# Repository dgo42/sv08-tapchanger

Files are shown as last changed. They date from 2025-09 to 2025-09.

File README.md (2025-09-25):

# Rebuild Sovol SV08 to use Tapchanger and up to 6 Toolheads
Sovol SV08 modification to use up to 6 print heads using TapChanger &amp; DragonBurner

1. First I've changed the LCD from the original to the BTT HDMI5. I've used the [BTT HDMI5 enclosure](https://www.printables.com/model/946297-sovol-sv08-btt-hdmi-5-v12-enclosure-compatible). I'm not really happy with this enclosure because of not working LCD buttons and too much backlash between enclosure and the cover frame, but it very robust and do the job. Other deal with this enclosure - it doesn't holds on the SV08 enclosure. You need TPU stopper [STL](https://github.com/dgo42/sv08-tapchanger/tree/main/stls/display) to prevent the screen enclosure to slide up and separate from the SV08 enclosure.

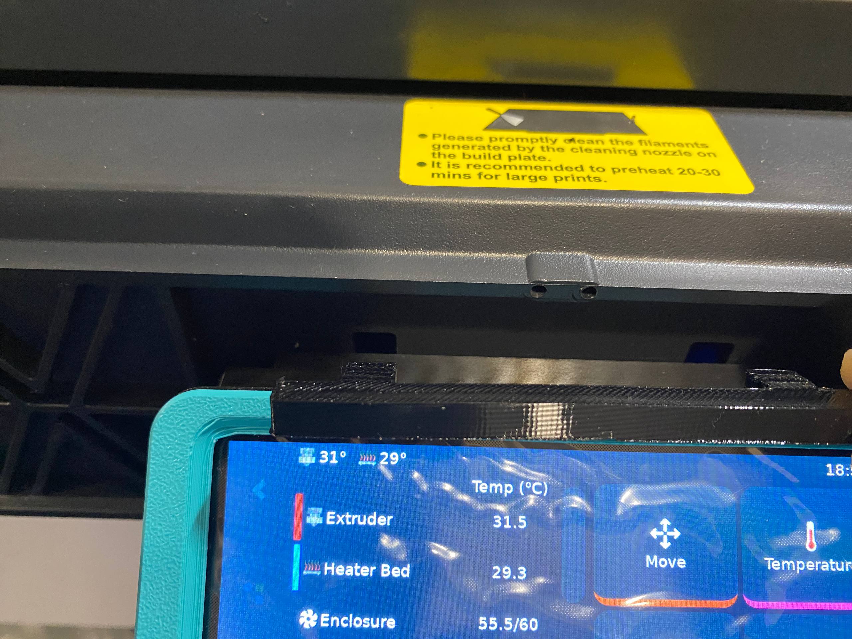
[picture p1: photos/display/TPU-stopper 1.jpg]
   [](https://github.com/dgo42/sv08-tapchanger/tree/main/photos/display/TPU-stopper%201.jpg?raw=true)
   [](https://github.com/dgo42/sv08-tapchanger/tree/main/photos/display/TPU-stopper%201.jpg?raw=true)
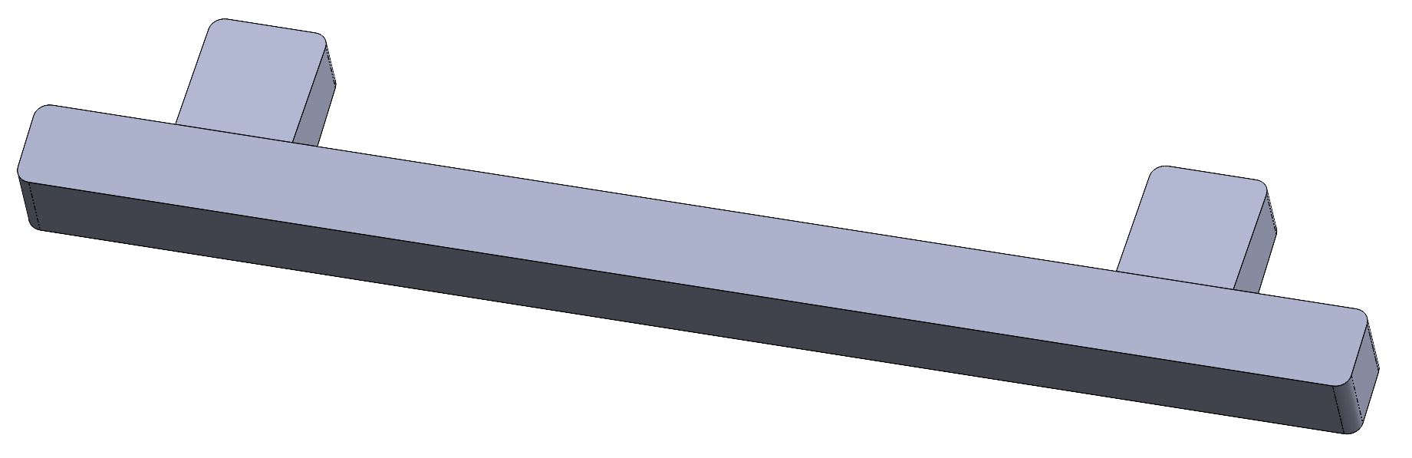
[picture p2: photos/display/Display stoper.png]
   [](https://github.com/dgo42/sv08-tapchanger/tree/main/photos/display/Display%20stoper.png?raw=true)
2. To connect BTT HDMI5 screen I've used original USB cable, but I've connected through [small USB hub](https://www.amazon.de/dp/B0BMXDGSGS) to one of USB type A connectors on the main board. HDMI connector on the main board is only one and it is accessible only from outside. So I've found [180° HDMI adapter](https://www.amazon.de/dp/B0C9DV6ZS) and [flat HDMI cable with 90° connector](https://www.amazon.de/dp/B07R4CPX7V). To use 180° HDMI adapter I needed to make some small cut in the SV08 enclosure.

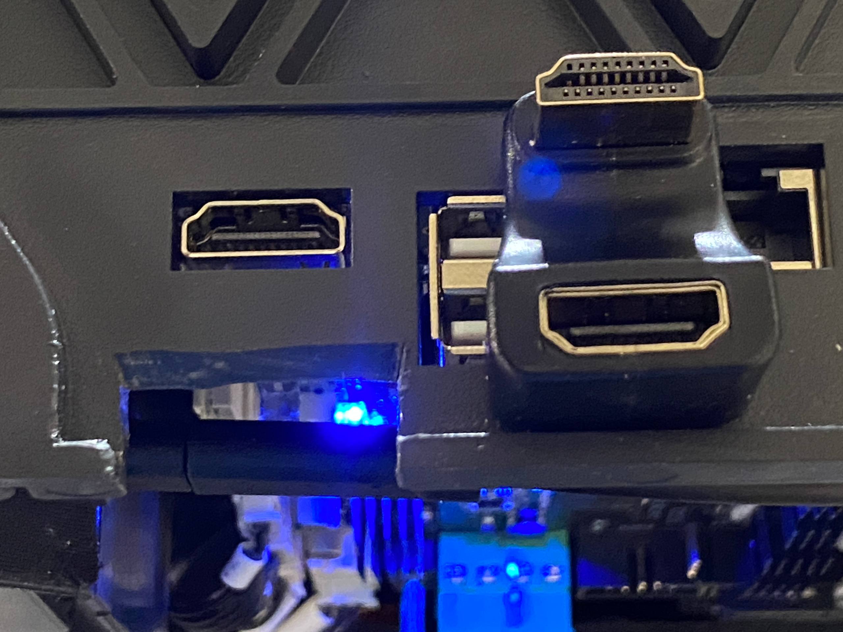
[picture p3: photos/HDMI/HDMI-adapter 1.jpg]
   [](https://github.com/dgo42/sv08-tapchanger/tree/main/photos/HDMI/HDMI-adapter%201.jpg?raw=true)
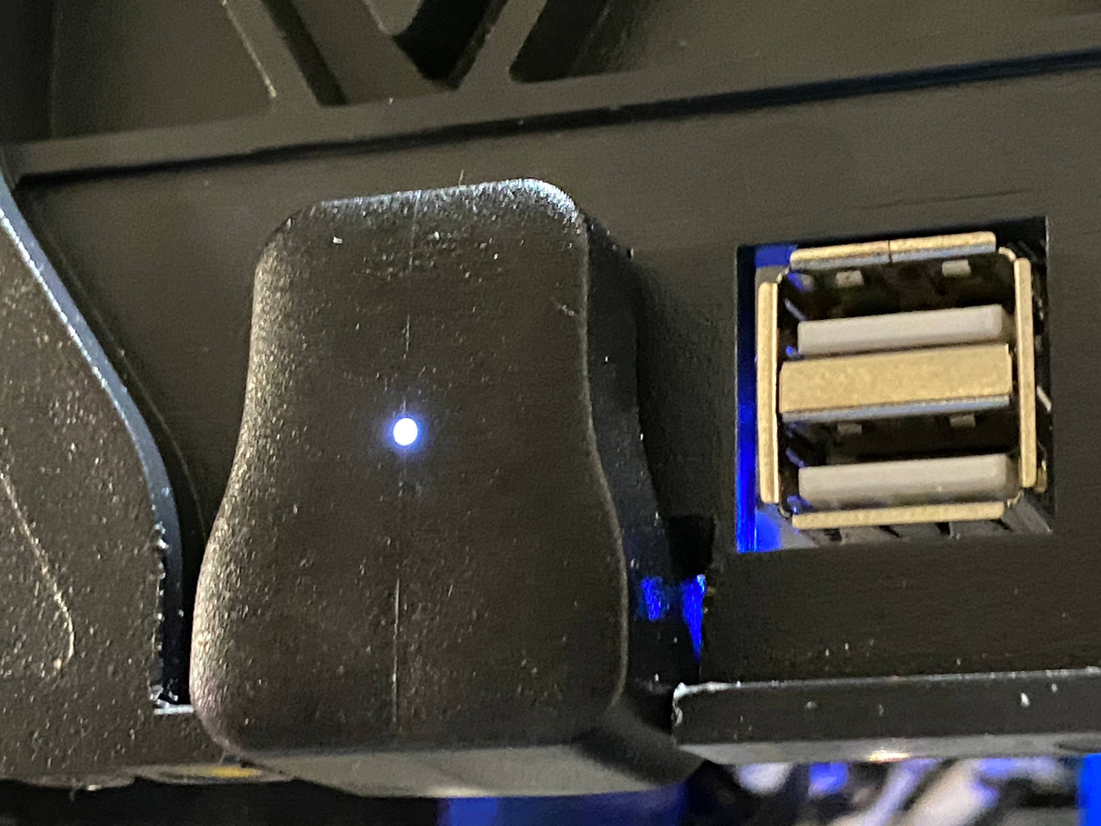
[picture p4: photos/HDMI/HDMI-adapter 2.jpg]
   [](https://github.com/dgo42/sv08-tapchanger/tree/main/photos/HDMI/HDMI-adapter%202.jpg?raw=true)
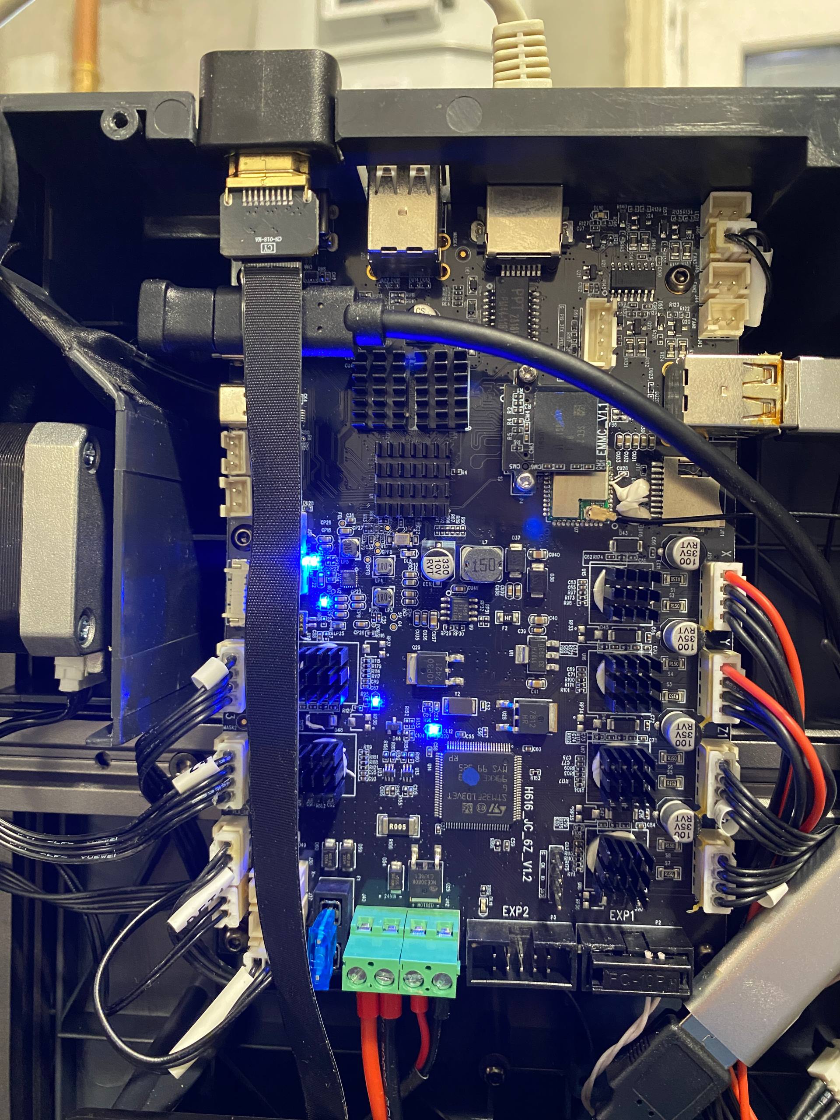
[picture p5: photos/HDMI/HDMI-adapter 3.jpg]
   [](https://github.com/dgo42/sv08-tapchanger/tree/main/photos/HDMI/HDMI-adapter%203.jpg?raw=true)
3. For the future use of up to 6 print heads the original PSU 24V 150W is not enough. I've buyed a cheaper Meanwell RSP-500-24 and made custom holders for [DIN rails](https://www.amazon.de/dp/B09VQ6KJ6H). You need about 266 mm DIN rail and following printed parts [STL](https://github.com/dgo42/sv08-tapchanger/tree/main/stls/psu-mount)

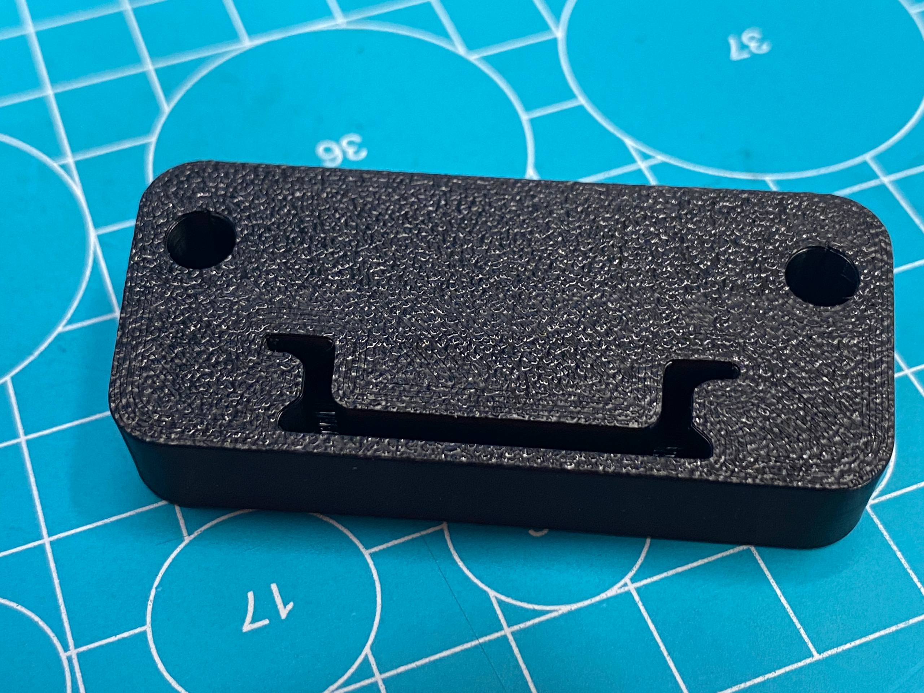
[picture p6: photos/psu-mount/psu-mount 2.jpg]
   [](https://github.com/dgo42/sv08-tapchanger/tree/main/photos/psu-mount/psu-mount%202.jpg?raw=true)
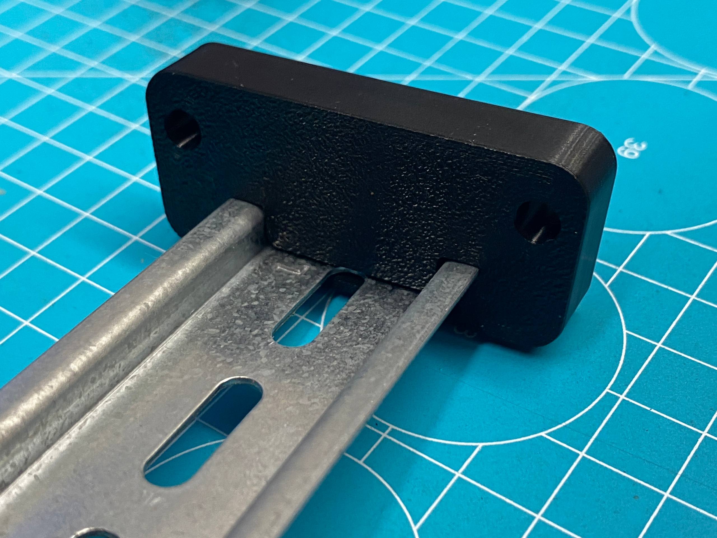
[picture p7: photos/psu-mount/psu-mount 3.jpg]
   [](https://github.com/dgo42/sv08-tapchanger/tree/main/photos/psu-mount/psu-mount%203.jpg?raw=true)
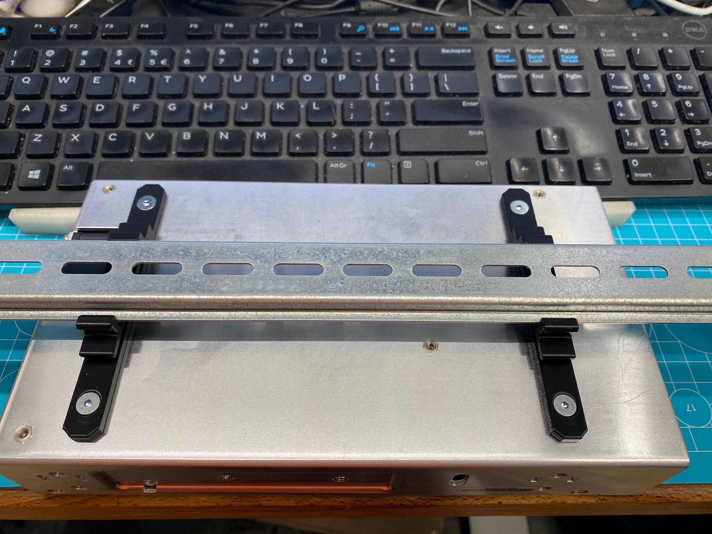
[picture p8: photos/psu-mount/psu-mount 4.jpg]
   [](https://github.com/dgo42/sv08-tapchanger/tree/main/photos/psu-mount/psu-mount%204.jpg?raw=true)
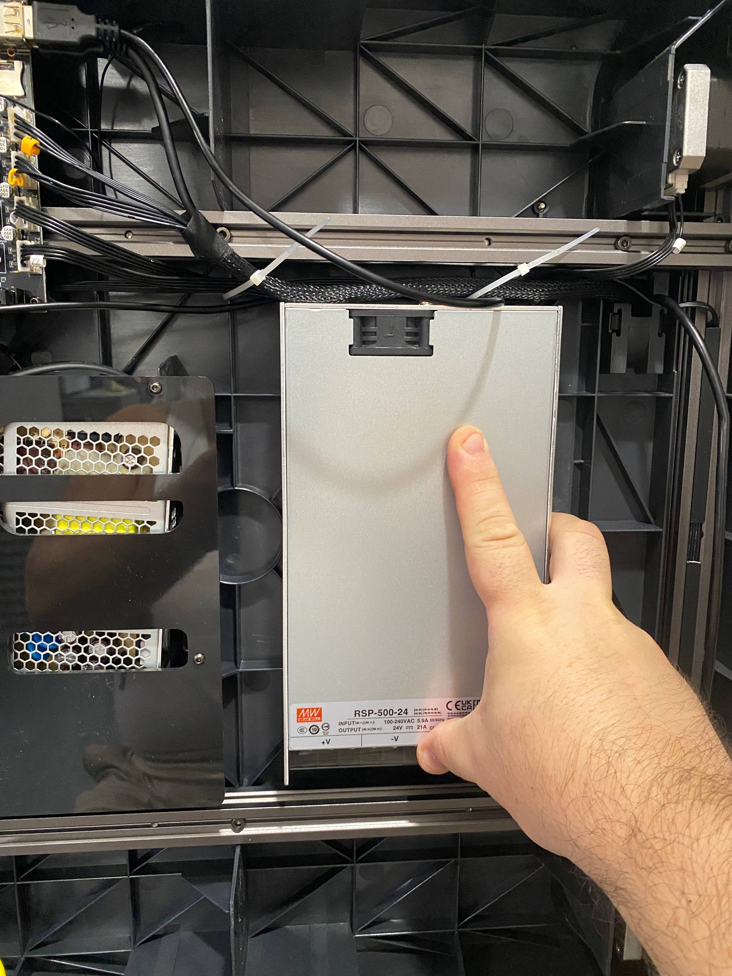
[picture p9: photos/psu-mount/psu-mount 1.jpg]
   [](https://github.com/dgo42/sv08-tapchanger/tree/main/photos/psu-mount/psu-mount%201.jpg?raw=true)
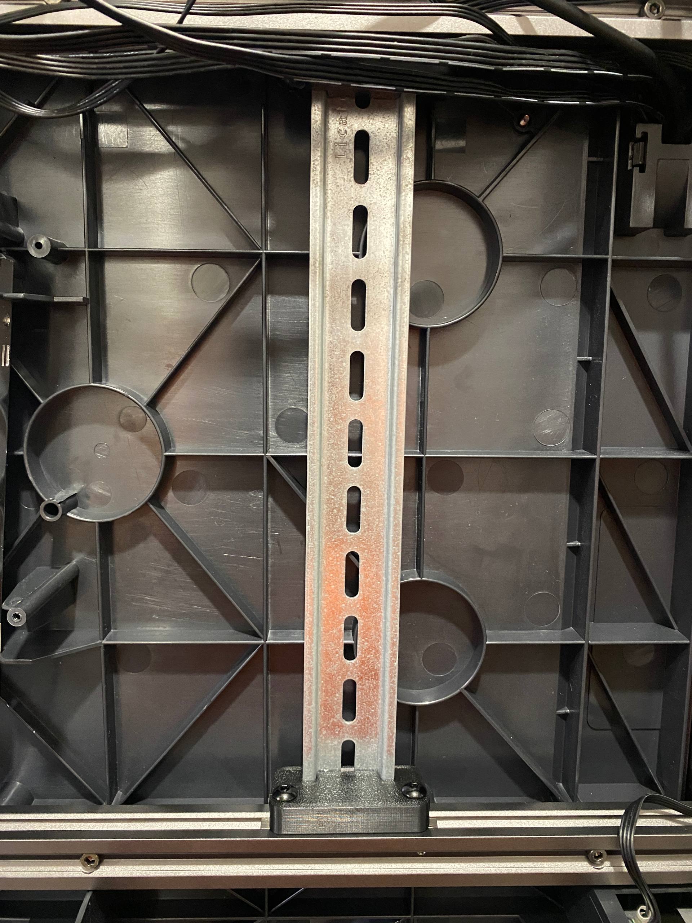
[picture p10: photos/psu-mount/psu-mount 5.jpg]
   [](https://github.com/dgo42/sv08-tapchanger/tree/main/photos/psu-mount/psu-mount%205.jpg?raw=true)
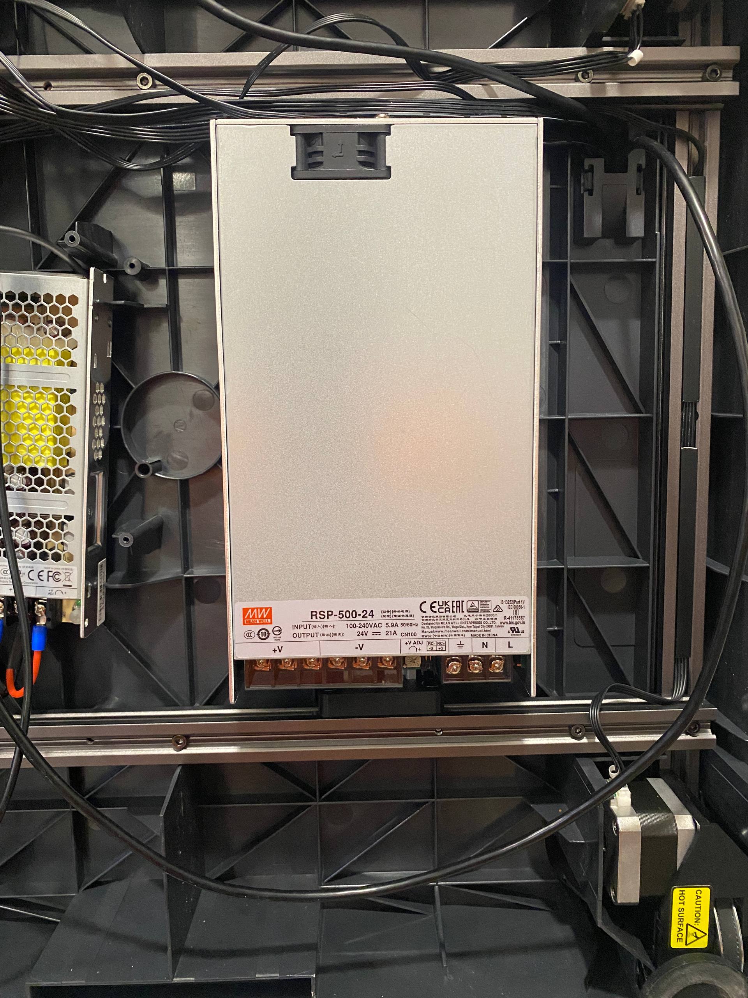
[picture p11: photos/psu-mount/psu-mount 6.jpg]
   [](https://github.com/dgo42/sv08-tapchanger/tree/main/photos/psu-mount/psu-mount%206.jpg?raw=true)
4. To organize the cables underneath I've used the voron deck support as a [cable organiser](https://github.com/dgo42/sv08-tapchanger/tree/main/stls/panels/cable-organiser_x4.stl)

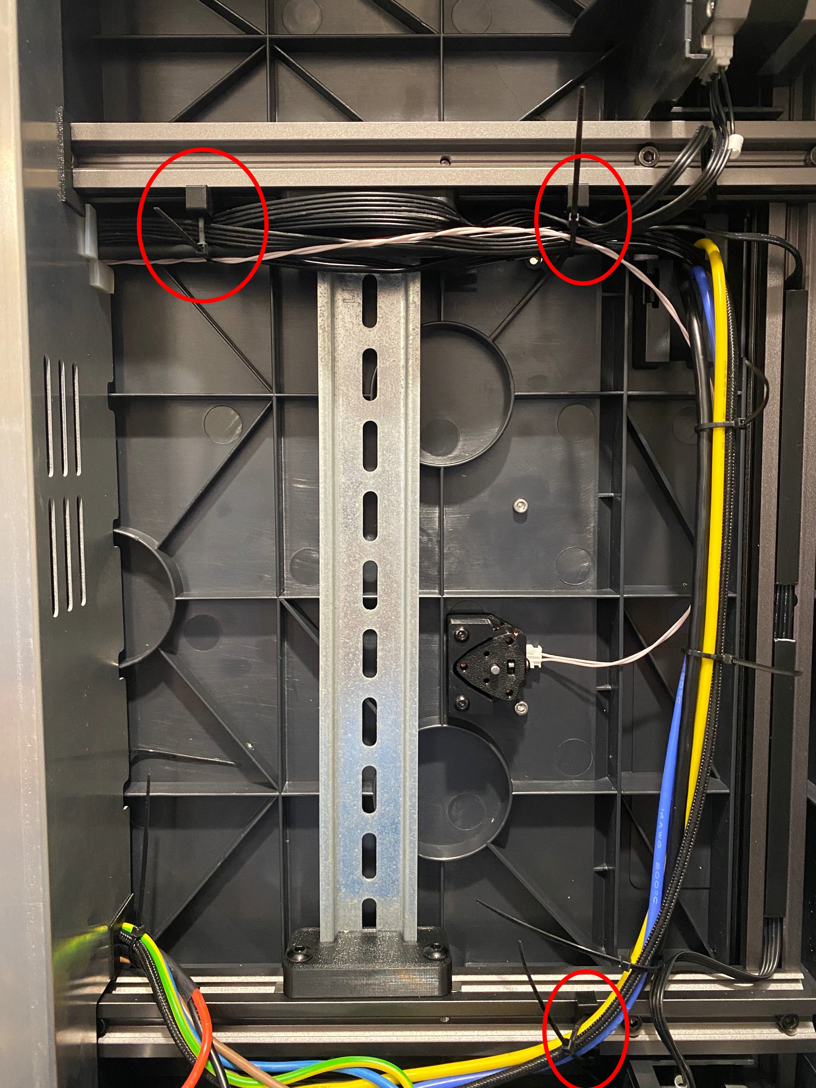
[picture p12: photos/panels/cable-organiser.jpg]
   [](https://github.com/dgo42/sv08-tapchanger/tree/main/photos/panels/cable-organiser.jpg?raw=true)
   
   To ptotect cables underneath aluminium cover I've created this two printed parts [STLs](https://github.com/dgo42/sv08-tapchanger/tree/main/stls/cable-protection) :

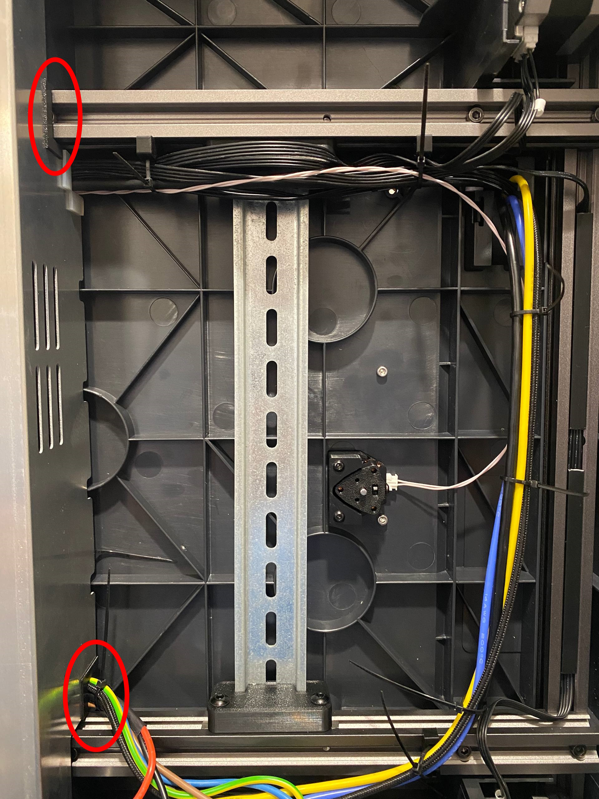
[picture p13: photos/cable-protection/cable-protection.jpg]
   [](https://github.com/dgo42/sv08-tapchanger/tree/main/photos/cable-protection/cable-protection.jpg?raw=true)
5. For different tasks Z-endstop, Z-calibration and XYZ multi printhead calibration I've used the Nudge sensor with 3 mm rod 55 mm long because prinhead has small moving distance behind the bed.
   * To mount the Nudge sensor and custom nozzle wiper I've made special jig to bore the mounting and Nudge rod holes [STL](https://github.com/dgo42/sv08-tapchanger/tree/main/stls/nudge/boring-jig.STL)
 
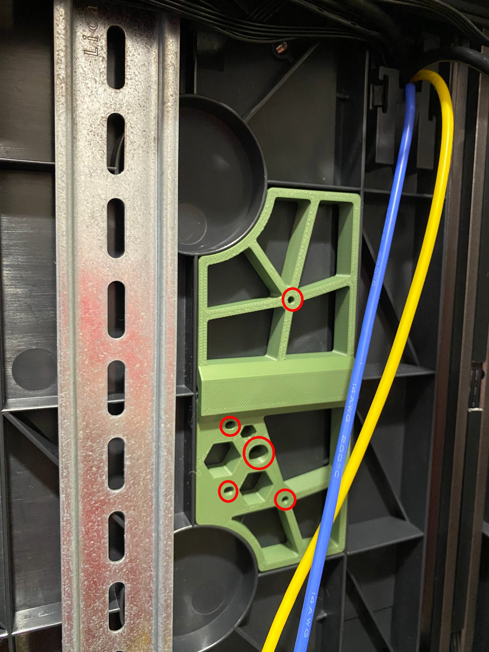
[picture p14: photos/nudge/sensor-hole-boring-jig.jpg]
      [](https://github.com/dgo42/sv08-tapchanger/tree/main/photos/nudge/sensor-hole-boring-jig.jpg?raw=true)
   * I've used modified Nudge sensor body to mount it to the top surface I've added 1mm so that JST XH connector is not outradged [STL](https://github.com/dgo42/sv08-tapchanger/tree/main/stls/nudge/nudge/nudge_2020_sovol.STL)
 
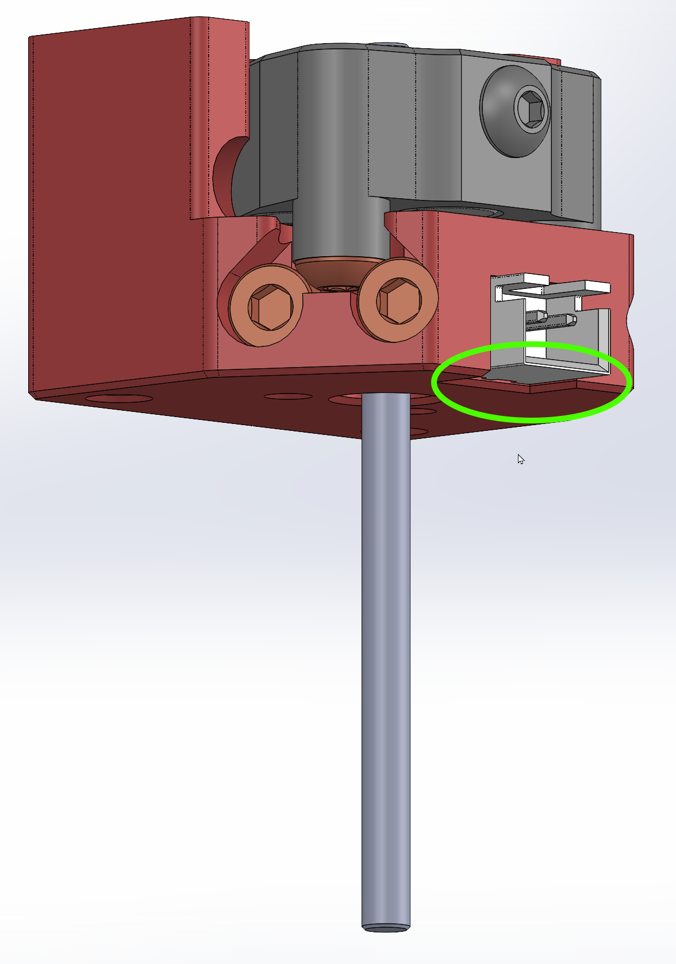
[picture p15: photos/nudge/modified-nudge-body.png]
      [](https://github.com/dgo42/sv08-tapchanger/tree/main/photos/nudge/modified-nudge-body.png?raw=true)
   * Nudge sensor mounted using two washers and 30mm iso 7380-1 screws, two 10mm DIN 912 screws holds other two corners of the nozzle wipper holder.
 
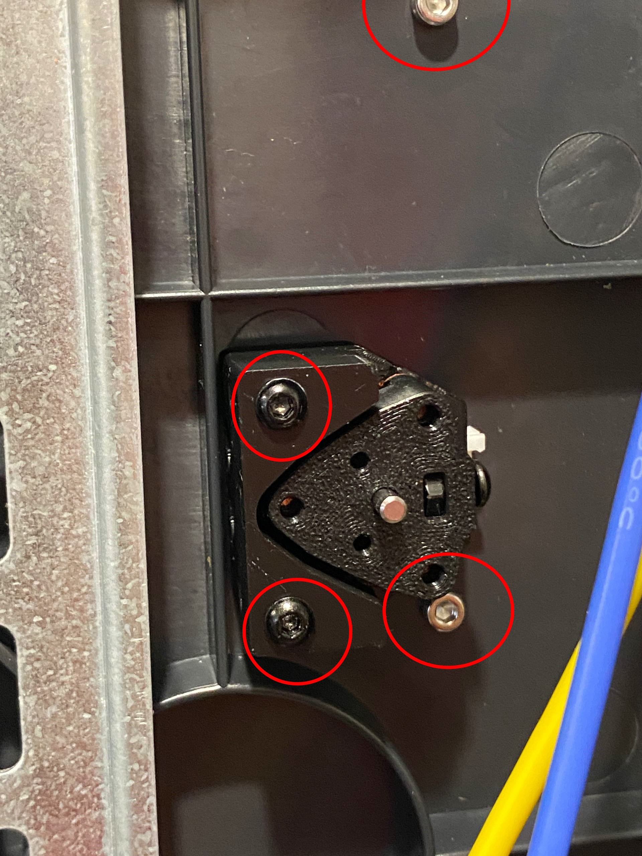
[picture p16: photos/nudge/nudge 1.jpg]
      [](https://github.com/dgo42/sv08-tapchanger/tree/main/photos/nudge/nudge%201.jpg?raw=true)
   * Bambulab A1 silicone nozzle wiper (for example https://www.amazon.de/dp/B0DZWXR1WL)
 
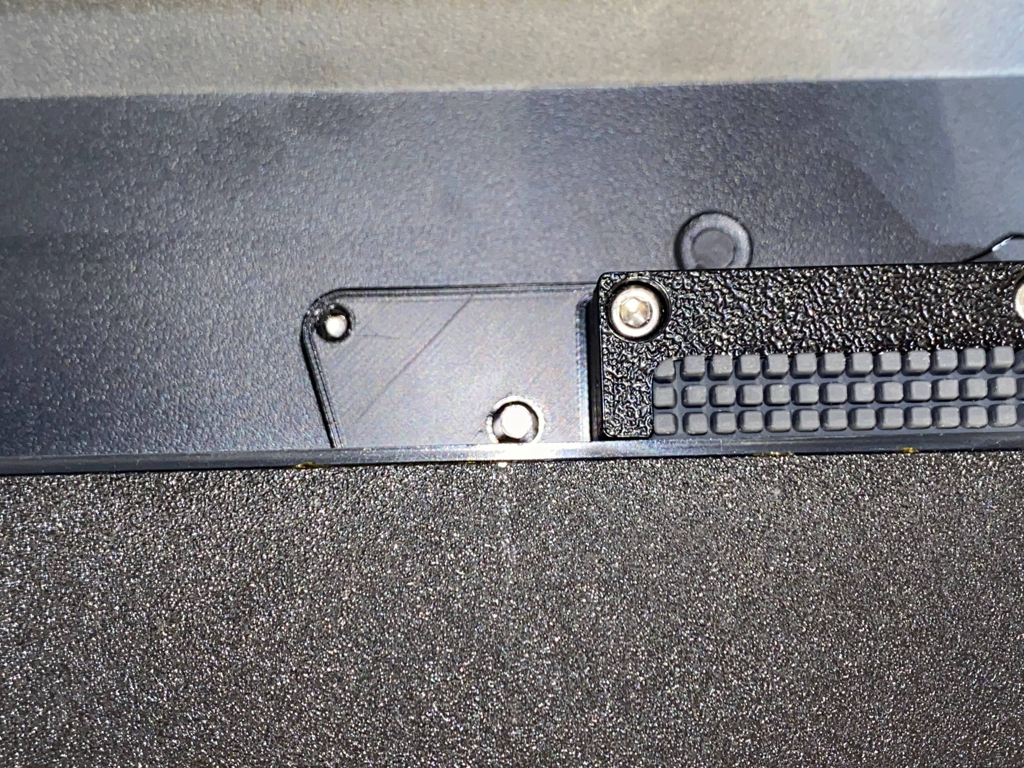
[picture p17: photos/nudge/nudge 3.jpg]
      [](https://github.com/dgo42/sv08-tapchanger/tree/main/photos/nudge/nudge%203.jpg?raw=true)
6. To use [Tapchanger](https://github.com/viesturz/tapchanger) I've disassembled cable harness from X-, Y- motor, camera and print head cables. To organize this cables I've used 27 chain links [10x15 cable chain](https://www.amazon.de/dp/B0991GWQ6P) and [connectors](https://makerworld.com/en/models/831830-sovol-sv08-chain-set-v2)

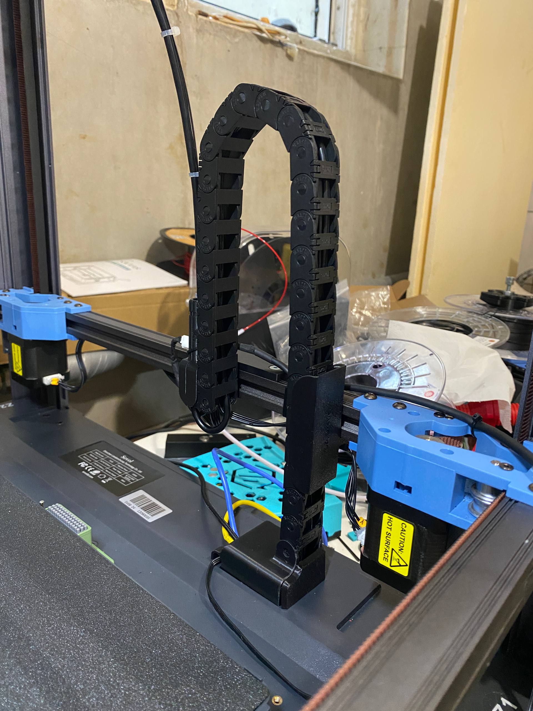
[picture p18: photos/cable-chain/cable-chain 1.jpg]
   [](https://github.com/dgo42/sv08-tapchanger/tree/main/photos/cable-chain/cable-chain%201.jpg?raw=true)
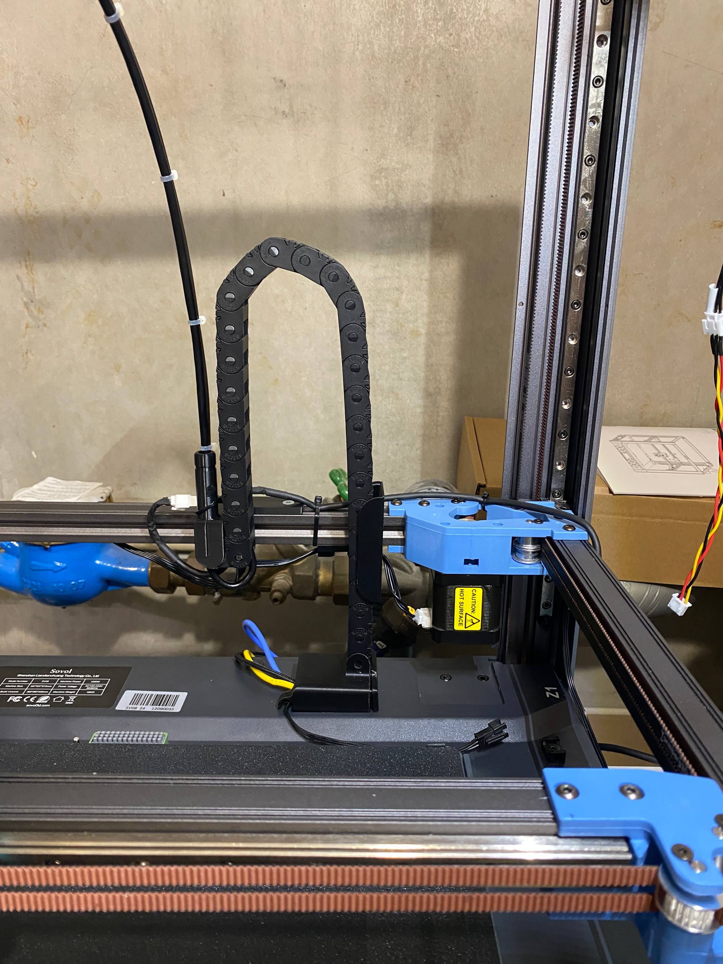
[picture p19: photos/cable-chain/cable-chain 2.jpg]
   [](https://github.com/dgo42/sv08-tapchanger/tree/main/photos/cable-chain/cable-chain%202.jpg?raw=true)
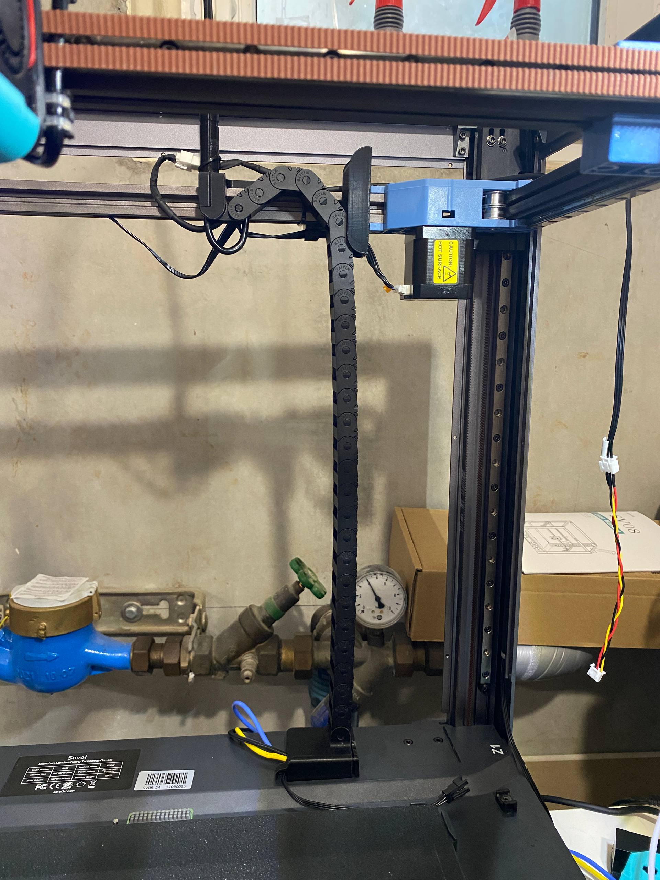
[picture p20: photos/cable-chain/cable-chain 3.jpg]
   [](https://github.com/dgo42/sv08-tapchanger/tree/main/photos/cable-chain/cable-chain%203.jpg?raw=true)
7. To use as much as possible movement distance behind the bed for using nudge sensor and nozzle wiper I've used Tapchanger [Shuttle](https://github.com/viesturz/tapchanger/blob/main/Tapchanger/STL/Shuttle/Shuttle.stl) without keeper to save additional 6mm. But usual MGN12H wagon has a 0.4 mm deeping which prevents efficient snuggle the belt between the wagon and the shuttle. I've developed MGN12H adapter, which adds only 0.4 mm additional space, but fills small deeping. It is printed with first layer height 0.2 mm and further layer 0.1 mm height, but it is also suitable to print all with 0.2 mm layer.  

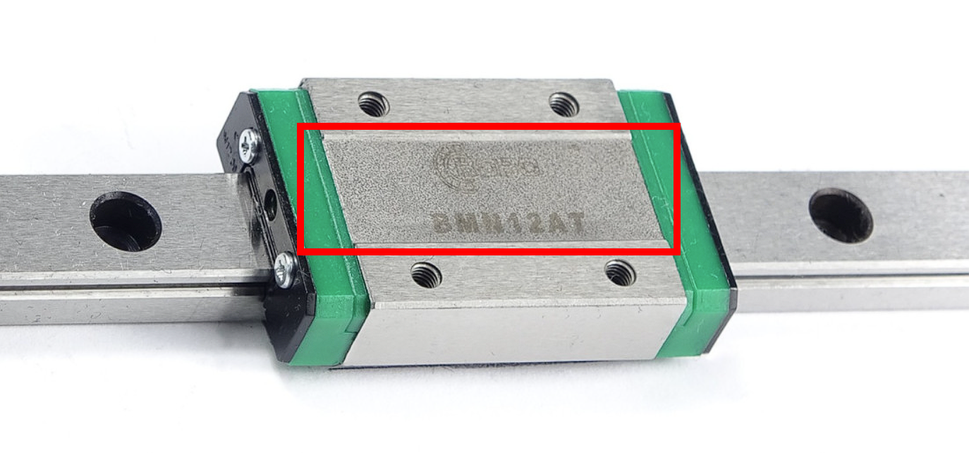
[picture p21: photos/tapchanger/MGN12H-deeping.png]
   [](https://github.com/dgo42/sv08-tapchanger/tree/main/photos/tapchanger/MGN12H-deeping.png?raw=true)
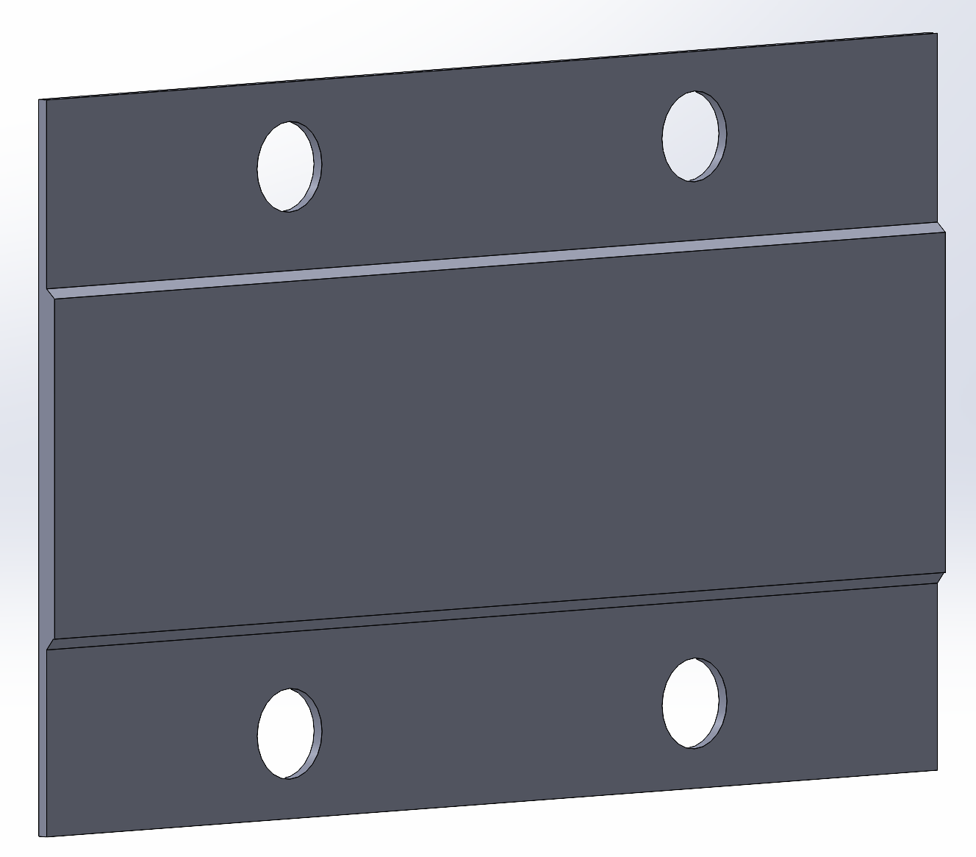
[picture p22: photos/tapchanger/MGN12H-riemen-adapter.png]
   [](https://github.com/dgo42/sv08-tapchanger/tree/main/photos/tapchanger/MGN12H-riemen-adapter.png?raw=true)

   Here you can see CAD reconstruction oh the problem. This is without adapter:

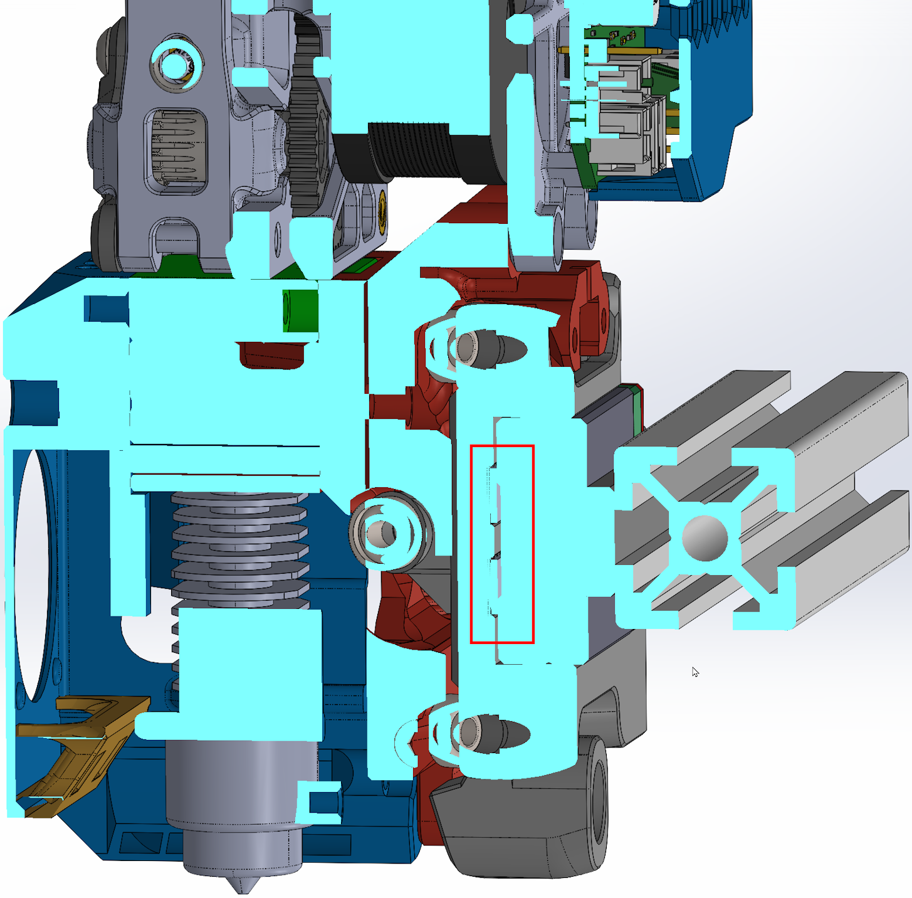
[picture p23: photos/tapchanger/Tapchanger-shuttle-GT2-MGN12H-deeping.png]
   [](https://github.com/dgo42/sv08-tapchanger/tree/main/photos/tapchanger/Tapchanger-shuttle-GT2-MGN12H-deeping.png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)
   
   And here with adapter:

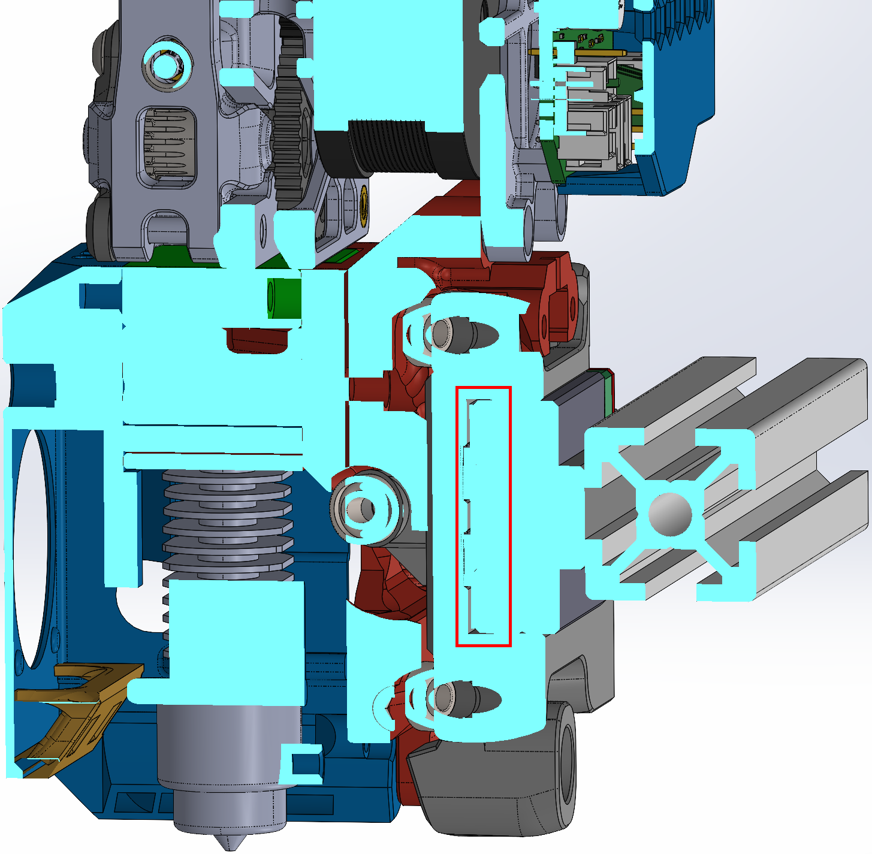
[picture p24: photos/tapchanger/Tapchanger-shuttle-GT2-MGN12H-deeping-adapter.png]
   [](https://github.com/dgo42/sv08-tapchanger/tree/main/photos/tapchanger/Tapchanger-shuttle-GT2-MGN12H-deeping-adapter.png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)

   Original belts are a little bit too short and therefore you need new belts. I've used Gates GT2 6mm. To replace and stretch the belts you can remove two timing belt pulleys. To stretch belts I use [belt helper](https://github.com/viesturz/tapchanger/tree/main/Tapchanger/STL/Jigs/BeltHelper) from tapchanger repo. 

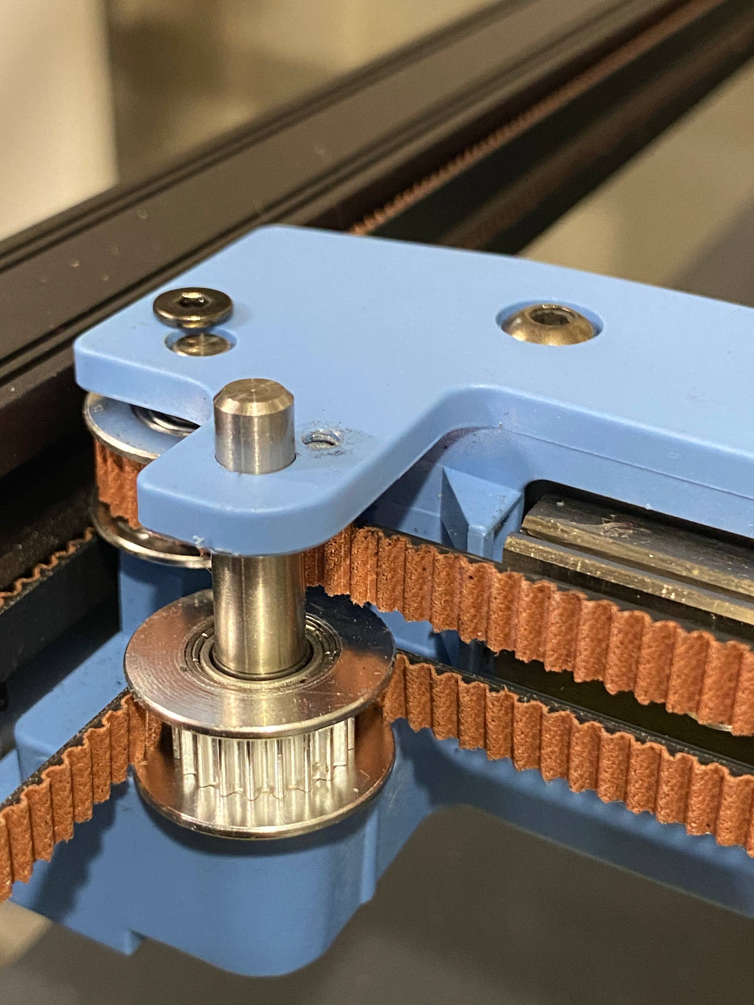
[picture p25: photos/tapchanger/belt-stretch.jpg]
   [](https://github.com/dgo42/sv08-tapchanger/tree/main/photos/tapchanger/belt-stretch.jpg?raw=true)

8. Used DragonBurner print head is about 8 mm shorter than original Sovol print head. That's why nozzle doesn't touch the bed even in lowest Z-position. To solve this problem I've made six 10 mm spacer between electronic bay and the bed assembly [STL](https://github.com/dgo42/sv08-tapchanger/tree/main/stls/bed/bed-spacer.STL). But this change make vertical movement bigger then original Sovol - 347 mm:

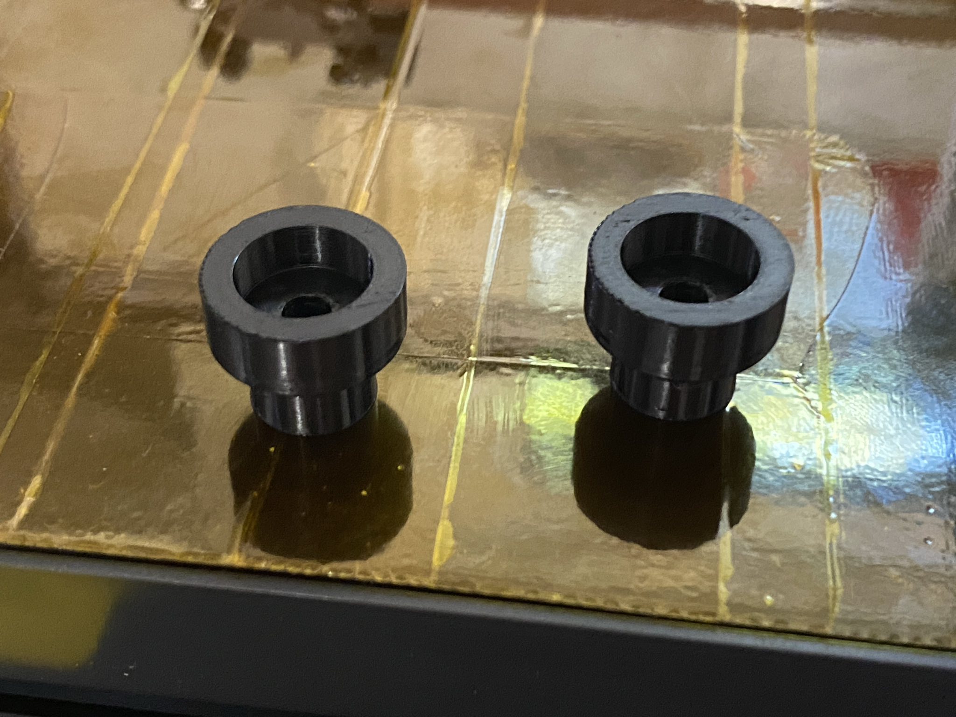
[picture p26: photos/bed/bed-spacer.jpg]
   [](https://github.com/dgo42/sv08-tapchanger/tree/main/photos/tapchanger/Tapchanger-shuttle-GT2-MGN12H-deeping.png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)
9. I was inspired by the videos from [chilicoke](https://www.youtube.com/@chilicoke) channel [3D Printer Nozzle Cam V2](https://www.youtube.com/watch?v=DgfCFKKtKLw) and modified my Voron 2.4 to use nozzle camera. I've found very good [5MP endoscope camera](https://www.aliexpress.com/item/1005007714189699.html) with auto-focus. It allows to focus from about 18 mm distance. I use variant with 2m with soft cable. But I'll use tapchanger, and therefore I've modified shuttle to use this camera [STL](https://github.com/dgo42/sv08-tapchanger/tree/main/stls/tapchanger/TapChanger-Rods-12-round-sovol.STL). Modified shuttle has also mount-point for camera cable holder [STL](https://github.com/dgo42/sv08-tapchanger/tree/main/stls/tapchanger/camera-cable-toolchanger-holder.STL) and stopper which reduces shuttle movement on the X-axe, to avoid camera tail to crash into gantry plastic parts. But the stopper allows to use entire bed - movement on the X/axe is about 358 mm. To avoid camera tail crash into X/Y motor as X-axe is on the maximal Y coordinate I've used side cuter to gently cut groove in the camera enclosure tail to route cable to the side. On the following photos you can see how to modify camera enclosure and route the camera cable:

   Camera enclosure should have cut out so, that cable may be bent and not protrude beyond the edge of the camera enclosure:

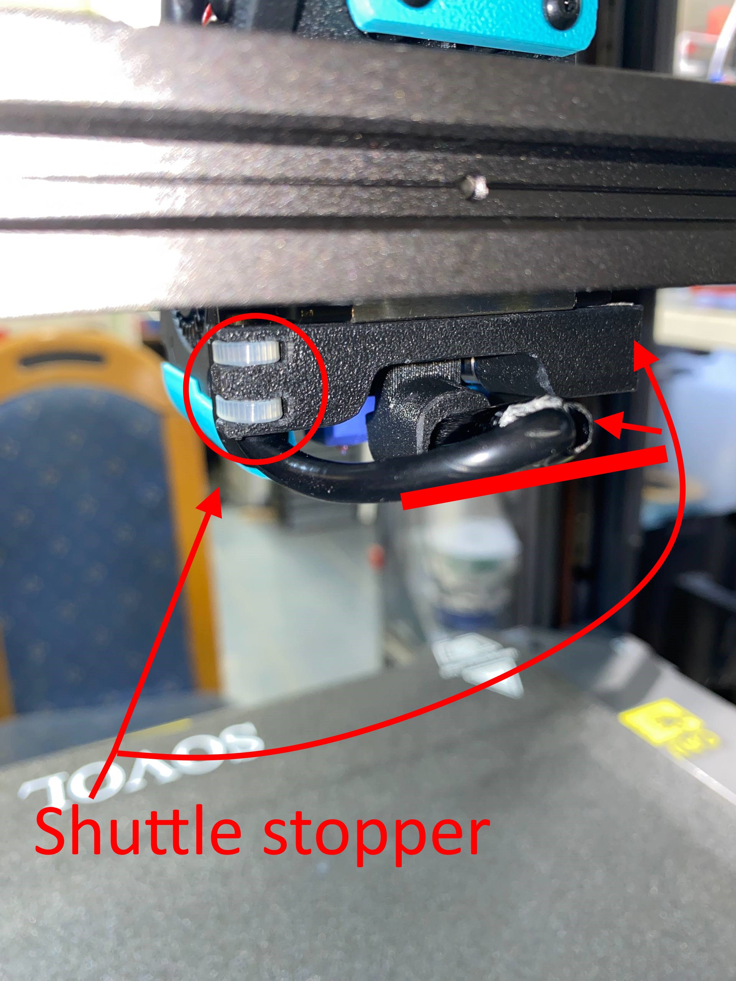
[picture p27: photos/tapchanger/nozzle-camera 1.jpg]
   [](https://github.com/dgo42/sv08-tapchanger/tree/main/photos/tapchanger/nozzle-camera%201.jpg?raw=true)

   Camera should be first pushed through the hole in camera cable holder underneath of the belts and cable should be tied on multiple places with cable ties. I've used 2.4mm width:

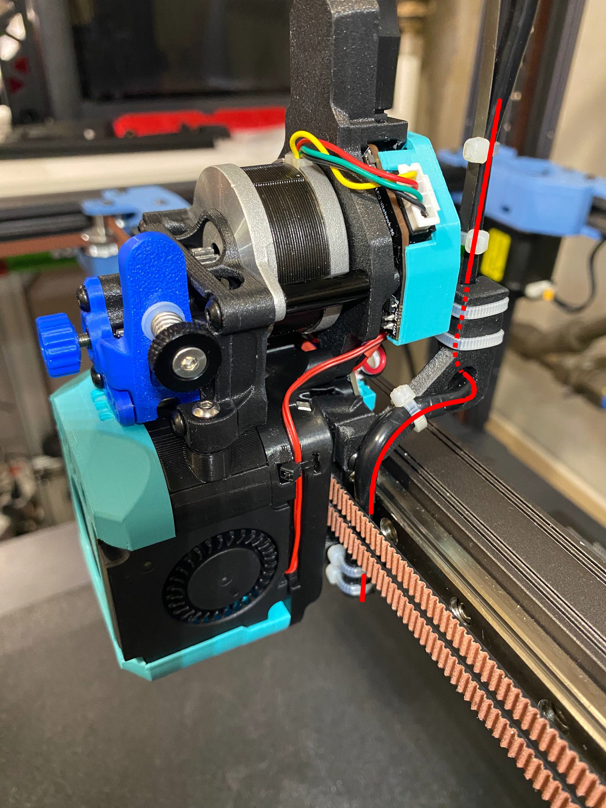
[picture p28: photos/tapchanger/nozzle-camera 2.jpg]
   [](https://github.com/dgo42/sv08-tapchanger/tree/main/photos/tapchanger/nozzle-camera%202.jpg?raw=true)
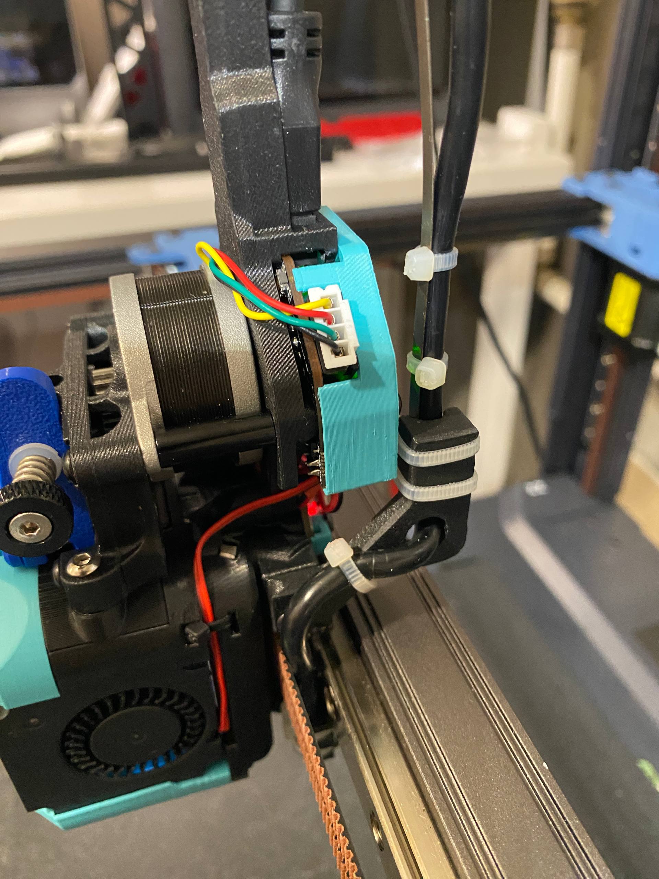
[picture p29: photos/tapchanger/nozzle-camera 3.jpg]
   [](https://github.com/dgo42/sv08-tapchanger/tree/main/photos/tapchanger/nozzle-camera%203.jpg?raw=true)

   I've mounted other side of the camera cable using cable chain connector instead of print head cable. You need approximately 45-50cm of "free" cable between both holders for free head movement. You can measure how much cable do you need moving the head into front left corner - the farthest point. Print heads cables will be organised using umbilical mount in the "hat". To prevent the cable from falling and to keep it in the shape of an arch I use suggested for tapchanger watch mainspring with section about 1mm<sup>2</sup> such as 0.3x3mm [Flat Spiral Coil](https://www.aliexpress.com/item/1005006731615186.html) tied with the cable using cable ties:

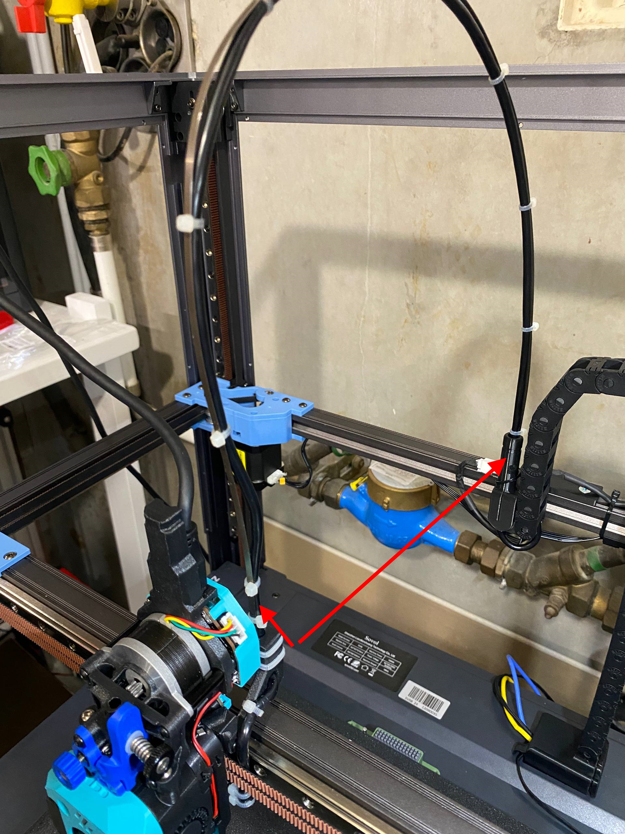
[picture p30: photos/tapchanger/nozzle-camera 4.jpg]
   [](https://github.com/dgo42/sv08-tapchanger/tree/main/photos/tapchanger/nozzle-camera%204.jpg?raw=true)

   Here is some sneak preview from nozzle camera from my Voron 2.4, it is 100% zoom:

   [](https://github.com/dgo42/sv08-tapchanger/tree/main/photos/camera/Voron-2.4-nozzle-cam-view.png?raw=true)

   ...and from Sovol SV08:

   [](https://github.com/dgo42/sv08-tapchanger/tree/main/photos/camera/Sovol-SV08-nozzle-cam-view.png?raw=true)

   Camera should be positioned horizontally using for example bed edge and fixed using superglue.
   
   To configure camera focus you can place under nozzle some object with small text and using following command select optimal focus setting. First you should find which camera corresponds to which linux device listing cameras by ID:
   
   `ls -la /dev/v4l/by-id/`
      
   [](https://github.com/dgo42/sv08-tapchanger/tree/main/photos/camera/camera-list.png?raw=true)
      
   `v4l2-ctl -d /dev/video0 -c focus_automatic_continuous=0,focus_absolute=700`

   After you've found a focus value, you can put it in crowsnest.cfg file adding `v4l2ctl: focus_automatic_continuous=0,focus_absolute=770` to corresponding camera section:
   
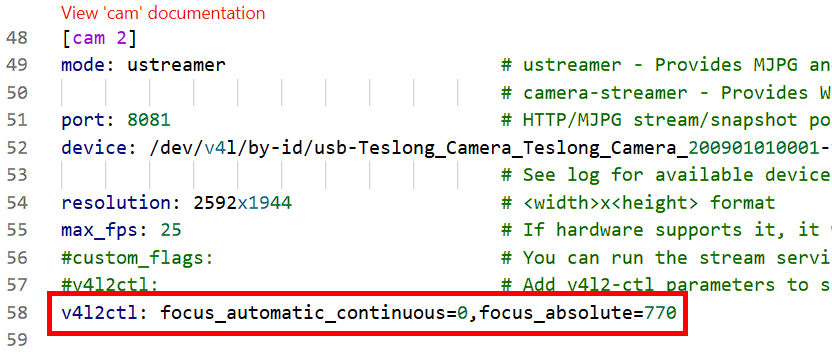
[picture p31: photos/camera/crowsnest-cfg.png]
   [](https://github.com/dgo42/sv08-tapchanger/tree/main/photos/camera/crowsnest-cfg.png?raw=true)
     
9. Last but not least to hold docking places for print heads I've found excellent solution [Sovol SV08 Tool Changer Extrusion Adapters](https://www.printables.com/model/902562-sovol-sv08-tool-changer-extrusion-adapters). But standard [Dock](https://github.com/viesturz/tapchanger/blob/main/Dock/Top/DragonBurner.stl) doesn't fit on the aluminium profile and more important the print head cant reach the dock position on the Y-axe. Therefore I've rebuilt the dock mount to fit both requirements [STL](https://github.com/dgo42/sv08-tapchanger/tree/main/stls/dock/DragonBurnerSovol.STL)

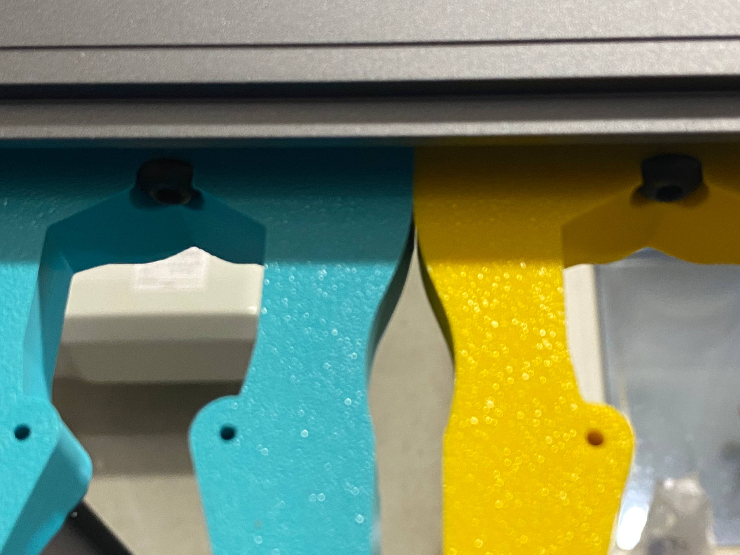
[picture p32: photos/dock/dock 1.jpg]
      [](https://github.com/dgo42/sv08-tapchanger/tree/main/photos/dock/dock%201.jpg?raw=true)
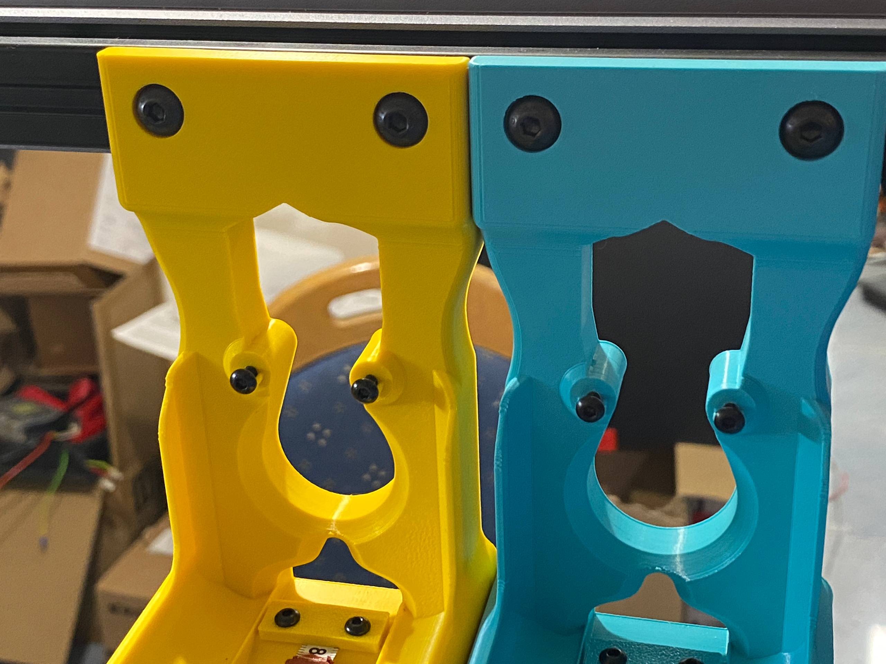
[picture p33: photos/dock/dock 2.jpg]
      [](https://github.com/dgo42/sv08-tapchanger/tree/main/photos/dock/dock%202.jpg?raw=true)

10. First I've used excellent guide from [Richard Rappetor](https://github.com/Rappetor) to update Sovol Klipper installation to the [mainline Klipper](https://github.com/Rappetor/Sovol-SV08-Mainline/tree/main). But due too removing original load cell Z-endstop sensor I don't use two of Sovol Python files (`probe_pressure.py`, `z_offset_calibration.py`)
   
   I very appreciate script to automatically update Klipper in hardware CPUs - I've copied it on my other Klipper printers.

11. In Klipper I use following addons (installation instruction are mostly to found in corresponding GitHub repos):
      1. [klipper-toolchanger](https://github.com/viesturz/klipper-toolchanger)
      2. [klipper_z_calibration](https://github.com/dgo42/klipper_z_calibration) from my fork. I've changed lower threshold for `switch_offset` config parameter to allow negative values down to -5.

   My current Klipper configuration you can found under [Config](https://github.com/dgo42/sv08-tapchanger/tree/main/klipper/config/)

12. Almost all parts are printed suing standard Voron slicer settings using **extrudr DuraPro ABS** filament. Only tapchanger shuttle and camera cable holder are printed from **extrudr DuraPro PC/PBT CF**. My DragonBurner addons I'll publish later in separate repo.
13. TODO:
 
      * exact BOM, however almost all bought parts are referenced in this manuell except of fasteners.
      * Slicer project file to exact print settings for different printed parts. Some of the printed parts needs tobe printed with support. I suggest to use "Normal" support with 0.1mm "Top Z distance" to make the part more reliable.

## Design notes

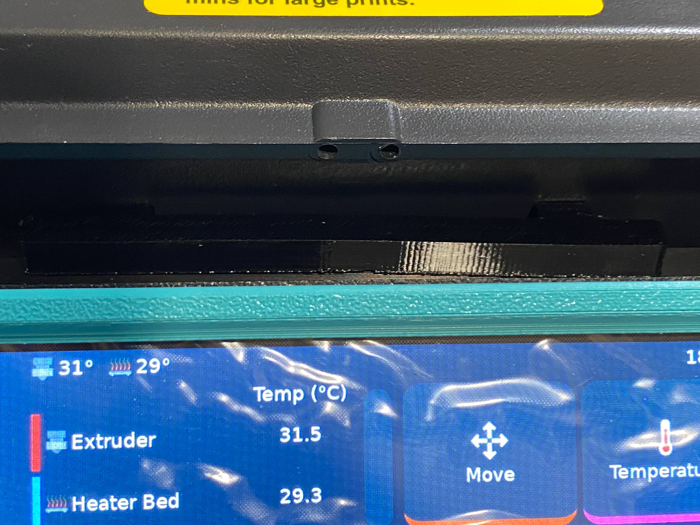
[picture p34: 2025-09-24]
photos/display/TPU-stopper 2.jpg

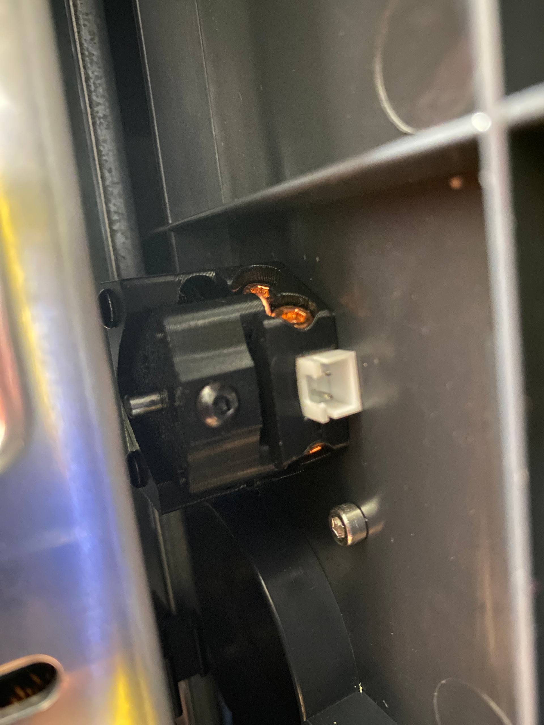
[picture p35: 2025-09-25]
photos/nudge/nudge 2.jpg

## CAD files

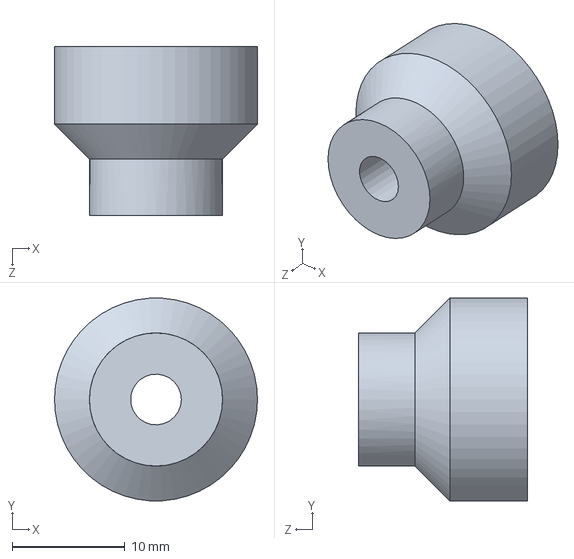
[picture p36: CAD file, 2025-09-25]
CAD/bed/bed-spacer.SLDPRT
18.0 x 18.0 x 15.0 mm

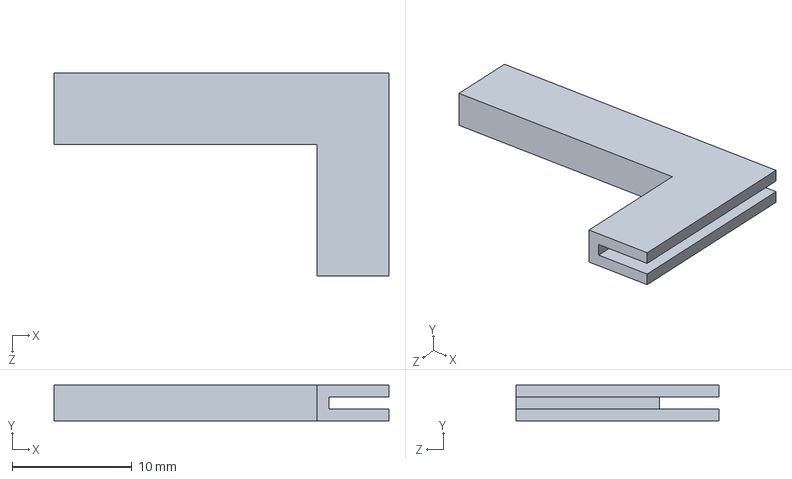
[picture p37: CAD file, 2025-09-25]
CAD/cable-protection/cable-protection.SLDPRT
28.0 x 3.00 x 17.0 mm

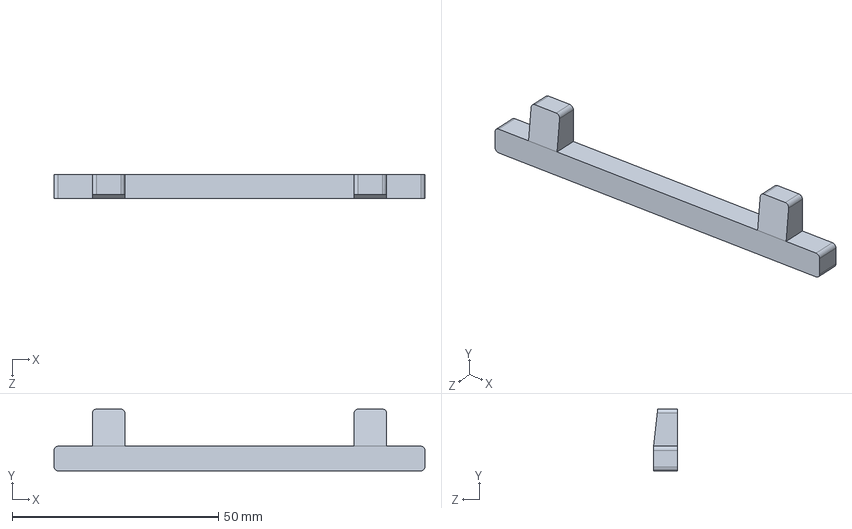
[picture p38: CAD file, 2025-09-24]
CAD/display/Display stoper.SLDPRT
90.0 x 15.0 x 5.80 mm

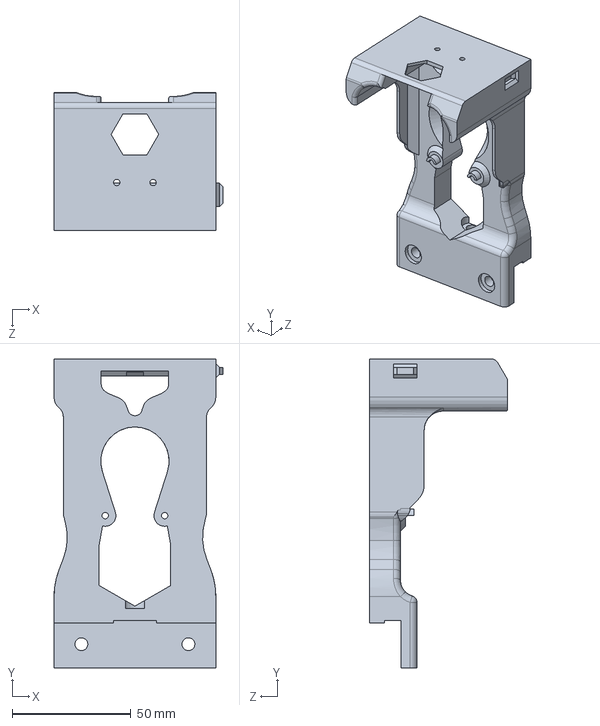
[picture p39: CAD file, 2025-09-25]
CAD/dock/DragonBurnerSovol.SLDPRT
71.0 x 129.9 x 58.0 mm

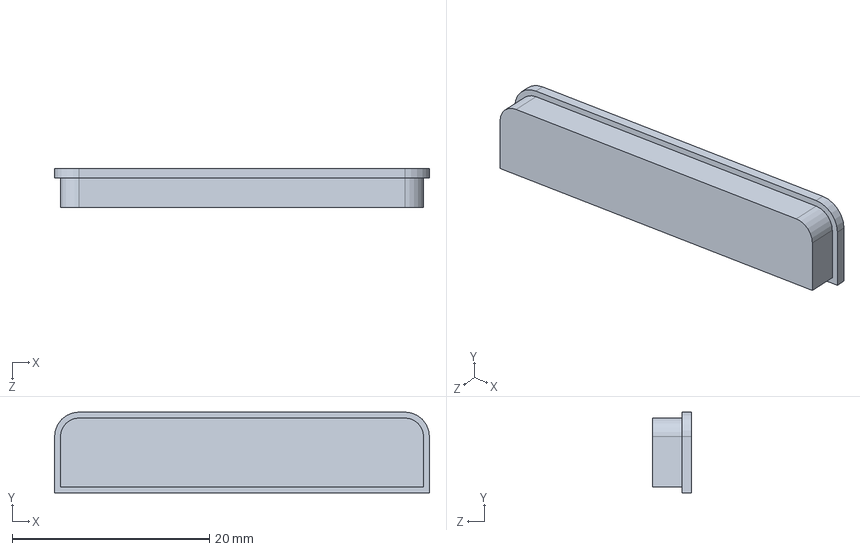
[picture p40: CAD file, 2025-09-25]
CAD/nudge/Bambulab A1 Wiper.SLDPRT
38.0 x 8.20 x 4.00 mm

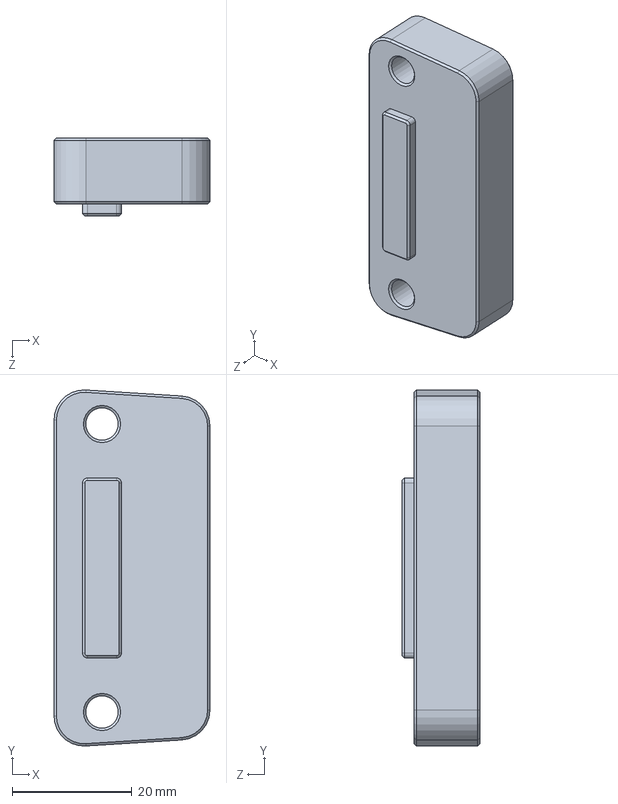
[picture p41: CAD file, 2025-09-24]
CAD/psu-mount/DIN Rail holder x2.SLDPRT
26.0 x 59.3 x 13.0 mm

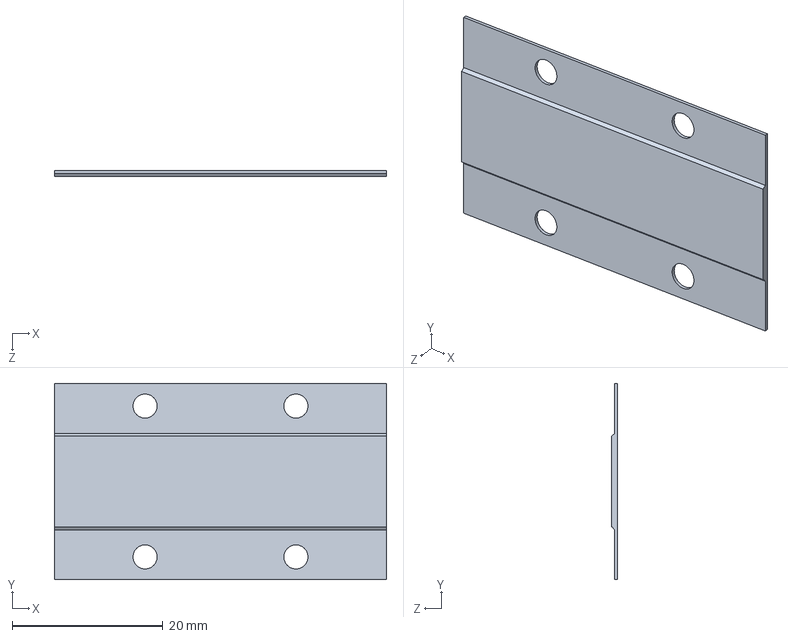
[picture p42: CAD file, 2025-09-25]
CAD/tapchanger/MGN12H_riemen_adapter.SLDPRT
44.0 x 26.0 x 0.8 mm

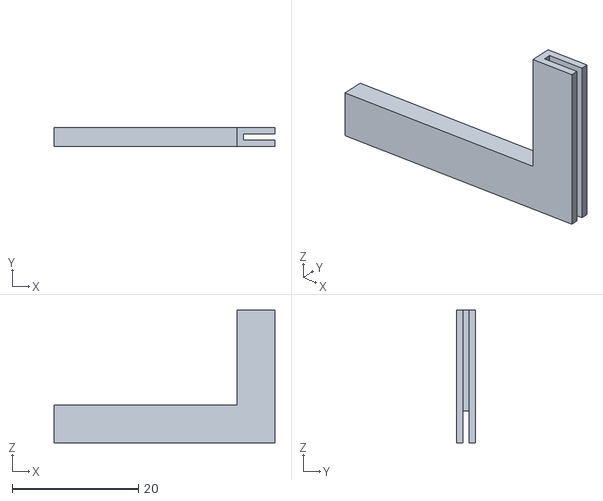
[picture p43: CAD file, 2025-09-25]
stls/cable-protection/cable-prot-33x16.STL
35.0 x 3.00 x 21.0

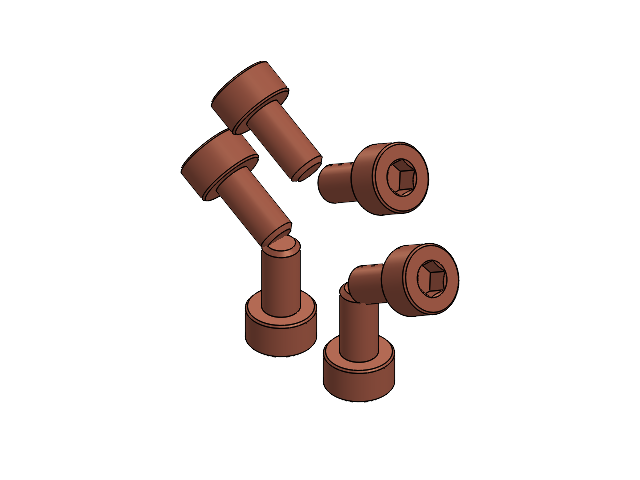
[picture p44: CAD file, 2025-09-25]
CAD/nudge/nudge/Horizontal SHCS.SLDASM
M3x6 SHCS x 6

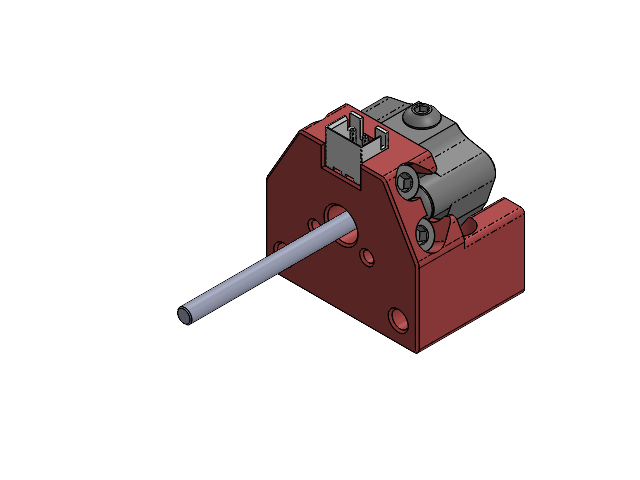
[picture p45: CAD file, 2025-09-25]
CAD/nudge/nudge/Nudge_2020_5mm.SLDASM
M3x6 SHCS x 6
6x3mm Magnet x 6
nudge_2020
M3_Hexnut
M3x10 BHCS v1
M3x6 BHCS v1 x 3
Wobbler-1
M3_pin_55mm
XH2.54-2P

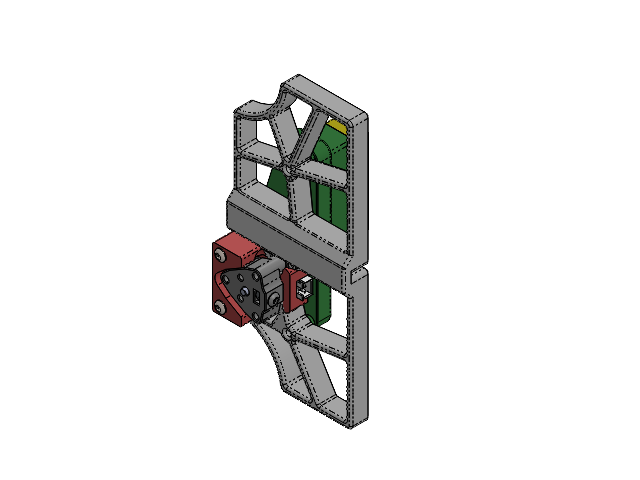
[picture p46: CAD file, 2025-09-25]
CAD/nudge/wiper-holder.SLDASM
wiper-holder_boring-jig x 2
wiper-clamp
Bambulab A1 Wiper
M3x6 SHCS x 6
6x3mm Magnet x 6
nudge_2020
M3_Hexnut
M3x10 BHCS v1
M3x6 BHCS v1 x 3
Wobbler-1
M3_pin_55mm
XH2.54-2P
ISO 7380 - M3 x 12 - 12N x 2
DIN 912 M3 x 8 --- 8N x 2

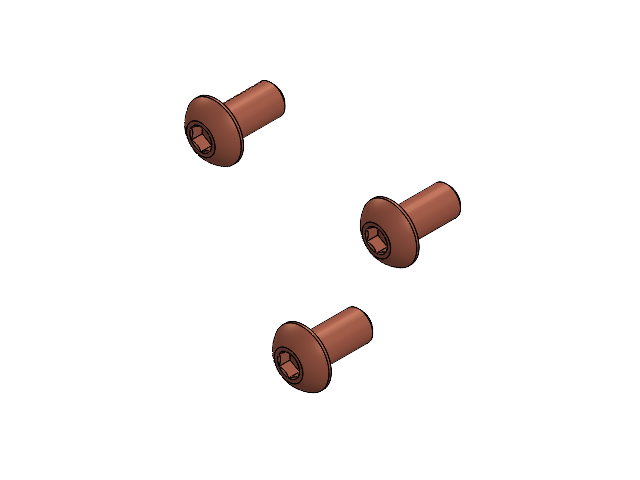
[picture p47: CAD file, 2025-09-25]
CAD/nudge/nudge/BHCS.SLDASM
M3x6 BHCS v1 x 3

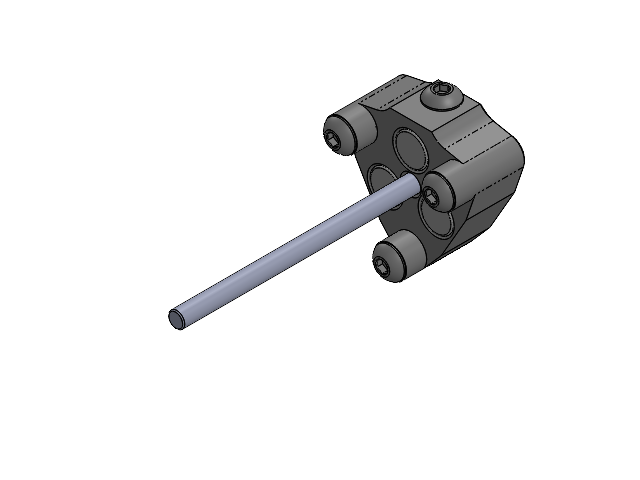
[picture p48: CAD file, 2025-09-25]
CAD/nudge/nudge/Wobbler.SLDASM
M3_Hexnut
M3x10 BHCS v1
M3x6 BHCS v1 x 3
6x3mm Magnet x 3
Wobbler-1
M3_pin_55mm

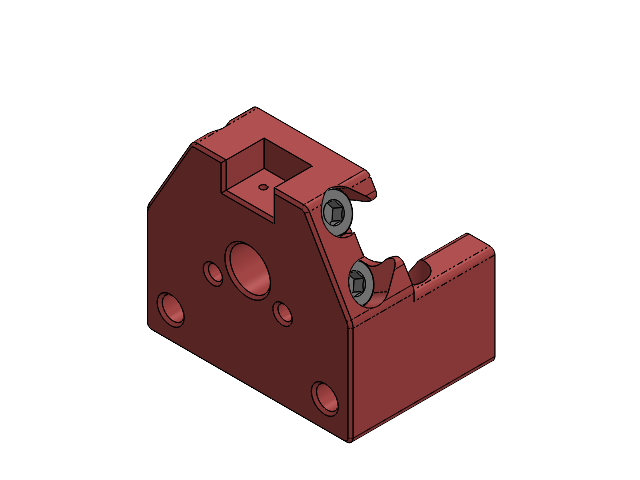
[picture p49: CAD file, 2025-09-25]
CAD/nudge/nudge/Mount.SLDASM
M3x6 SHCS x 6
6x3mm Magnet x 3
nudge_2020

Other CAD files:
CAD/nudge/nudge/JST XH 2pin.SLDASM
CAD/nudge/nudge/M3 Hexnut.SLDASM
CAD/nudge/nudge/XH2.54-2P.SLDASM
CAD/nudge/nudge/Magnets.SLDASM
CAD/nudge/nudge/6x3mm Magnet.SLDPRT
CAD/nudge/nudge/M3_Hexnut.SLDPRT
CAD/nudge/nudge/M3_pin_55mm.SLDPRT
CAD/nudge/nudge/M3x10 BHCS v1.SLDPRT
CAD/nudge/nudge/M3x6 BHCS v1.SLDPRT
CAD/nudge/nudge/M3x6 SHCS.SLDPRT
CAD/nudge/nudge/Magnets (1).SLDASM
CAD/nudge/nudge/Mount-0.SLDPRT
CAD/nudge/nudge/Retention Screw.SLDASM
CAD/nudge/nudge/Wobbler-1.SLDPRT
CAD/nudge/nudge/XH2.54-2P.SLDPRT
CAD/nudge/nudge/nudge_2020.SLDPRT
CAD/nudge/wiper-clamp.SLDPRT
CAD/nudge/wiper-holder_boring-jig.SLDPRT
CAD/psu-mount/RSP-500 DIN Bracket low x2.SLDPRT
CAD/tapchanger/TapChanger-Rods-12.SLDPRT
CAD/tapchanger/camera-cable-toolchanger-holder.SLDPRT
stls/bed/bed-spacer.STL
stls/cable-protection/cable-prot-23x12.STL
stls/display/Display stoper.STL
stls/dock/DragonBurnerSovol.STL
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

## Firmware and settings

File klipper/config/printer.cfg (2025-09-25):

[include fluidd.cfg]
[include timelapse.cfg]
#[include get_ip.cfg]
[include plr.cfg]
[include Macro.cfg]
#[include moonraker_obico_macros.cfg]

[mcu]      
serial: /dev/serial/by-id/usb-Klipper_stm32f103xe_36FFD805334D413222680551-if00
restart_method: command     

[include birds-nest.cfg]

[include toolchanger.cfg]
[include macros.cfg]
[include calibrate_offsets.cfg]
[include homing.cfg]
[include tool_detection.cfg]
[include z-calibration.cfg]
[include user_variables.cfg]

[include bed_mesh.cfg]

[include T0.cfg]
## Uncomment this to allow second print head. Next print heads should be configured analog to T1
#[include T1.cfg]

[exclude_object]

[temperature_sensor STM32_temp]         
sensor_type: temperature_mcu
min_temp:0
max_temp:100

[temperature_sensor H616_temp]     
sensor_type: temperature_host
min_temp: 0
max_temp: 110

[virtual_sdcard] 
path:/home/sovol/printer_data/gcodes/

[pause_resume]

[printer]
kinematics: corexy           
max_velocity: 700            
max_accel: 40000             
#max_accel_to_decel: 10000     
max_z_velocity: 30           
max_z_accel: 500
square_corner_velocity: 5.0  

[input_shaper]
damping_ratio_x: 0.001
damping_ratio_y: 0.001
shaper_type_x = mzv
shaper_freq_x = 65.2
shaper_type_y = mzv
shaper_freq_y = 40.4

[bed_mesh]
speed: 500                   
horizontal_move_z: 2         
mesh_min: 10, 10              
mesh_max: 345, 345            
probe_count: 9,9             
algorithm: bicubic   
bicubic_tension: 0.4
zero_reference_position: 177.5, 177.5
split_delta_z: 0.0125 #0.016
mesh_pps:3, 3
adaptive_margin: 5
fade_start: 0
fade_end: 10
fade_target: 0

[quad_gantry_level]          
gantry_corners:              
    -60,-30
    420,470
points:
    25,40
    25,320
    330,330
    330,40
speed: 500                   
horizontal_move_z: 5       
retry_tolerance: 0.010 #0.05     
retries: 5                  
max_adjust: 10 #30              

[stepper_x]
step_pin: PE2
dir_pin: !PE0
enable_pin: !PE3
rotation_distance: 40         
microsteps: 64 #16                
full_steps_per_rotation:200   
endstop_pin: tmc2209_stepper_x: virtual_endstop              
position_min: 0               
position_endstop: 0         
position_max: 358             
homing_speed: 30              
homing_retract_dist: 0
homing_positive_dir: False     
#--------------------------------------------------------------------
[tmc2209 stepper_x]
uart_pin: PE1
interpolate: False #True             
run_current: 1.061 #1.5
#hold_current: 1.061 #1.5            
sense_resistor: 0.150         
#stealthchop_threshold: 0      
uart_address:3
driver_sgthrs: 70 #65
diag_pin: PE15
driver_TBL: 1
driver_TOFF: 3
driver_HSTRT: 7
driver_HEND: 5

[stepper_y]
step_pin: PB8
dir_pin: !PB6
enable_pin: !PB9
rotation_distance: 40         
microsteps: 64 #16                
full_steps_per_rotation:200   
endstop_pin: tmc2209_stepper_y: virtual_endstop              
position_min: -5               
position_endstop: 361         
position_max: 361            
homing_speed: 30              
homing_retract_dist: 0
homing_positive_dir: true     
#--------------------------------------------------------------------
[tmc2209 stepper_y]
uart_pin: PB7
interpolate: False #True             
run_current: 1.061 #1.5
#hold_current: 1.061 #1.5             
sense_resistor: 0.150         
#stealthchop_threshold: 0      
uart_address:3
driver_sgthrs: 70 #75 #65
diag_pin: PE13
driver_TBL: 1
driver_TOFF: 3
driver_HSTRT: 7
driver_HEND: 5

[stepper_z] #motherboard：Z3 
step_pin:PC0    
dir_pin:PE5    
enable_pin:!PC1    
rotation_distance: 40         
gear_ratio: 80:12             
microsteps: 64 #16
#endstop_pin: probe:z_virtual_endstop           
# Nudge
endstop_pin: ^!PD8
position_max: 347             
position_min: -5              
#position_endstop: 0
position_endstop: 0.49
homing_speed: 10.0
homing_retract_dist: 1.0
homing_retract_speed: 15.0
second_homing_speed: 10.0
#--------------------------------------------------------------------
[tmc2209 stepper_z]
uart_pin: PE6 
interpolate: false #true             
run_current: 0.566 #0.58          
#hold_current: 0.566 #0.58         
sense_resistor: 0.150       
stealthchop_threshold: 999999 
uart_address:3
#driver_TBL: 1
#driver_TOFF: 3
#driver_HSTRT: 0
#driver_HEND: 2

[stepper_z1] ##motherboard：Z1
step_pin:PD3  
dir_pin:!PD1 
enable_pin:!PD4 
rotation_distance: 40         
gear_ratio: 80:12            
microsteps: 64 #16        
#--------------------------------------------------------------------
[tmc2209 stepper_z1]
uart_pin:PD2  
interpolate: false #true             
run_current: 0.566 #0.58          
#hold_current: 0.566 #0.58         
sense_resistor: 0.150  
stealthchop_threshold: 999999 
uart_address:3
#driver_TBL: 1
#driver_TOFF: 3
#driver_HSTRT: 0
#driver_HEND: 2

[stepper_z2] ##motherboard：Z2
step_pin:PD7
dir_pin:PD5   
enable_pin:!PB5
rotation_distance: 40         
gear_ratio: 80:12             
microsteps: 64 #16          
#--------------------------------------------------------------------
[tmc2209 stepper_z2]
uart_pin:PD6  
interpolate: false #true             
run_current: 0.566 #0.58          
#hold_current: 0.566 #0.58         
sense_resistor: 0.150   
stealthchop_threshold: 999999 
uart_address:3
#driver_TBL: 1
#driver_TOFF: 3
#driver_HSTRT: 0
#driver_HEND: 2

[stepper_z3] ##motherboard：Z4
step_pin:PD11 
dir_pin:!PD9 
enable_pin:!PD12   
rotation_distance: 40         
gear_ratio: 80:12             
microsteps: 64 #16       
#--------------------------------------------------------------------
[tmc2209 stepper_z3]
uart_pin:PD10    
interpolate: false #true             
run_current: 0.566 #0.58          
#hold_current: 0.566 #0.58         
sense_resistor: 0.150
stealthchop_threshold: 999999 
uart_address:3
#driver_TBL: 1
#driver_TOFF: 3
#driver_HSTRT: 0
#driver_HEND: 2

[thermistor my_thermistor_e]
temperature1:25
resistance1:110000
temperature2:100
resistance2:7008
temperature3:220
resistance3:435

[verify_heater extruder]      
max_error: 120                
check_gain_time:30           
hysteresis: 5                
heating_gain: 2               

[filament_switch_sensor filament_sensor]
pause_on_runout: True
event_delay: 3.0
pause_delay: 0.5
switch_pin: PE9

[thermistor my_thermistor]
temperature1:25
resistance1:100000
temperature2:50
resistance2:18085.4
temperature3:100
resistance3:5362.6

[heater_bed]
heater_pin:PA0
sensor_type: my_thermistor  
sensor_pin: PC5
max_power: 1.0               
min_temp: 5                  
max_temp: 105                
control : pid
# original
#pid_kp : 73.571
#pid_ki : 1.820
#pid_kd : 783.849
# calibrated
pid_kp : 65.160
pid_ki : 0.840
pid_kd : 783.849

[verify_heater heater_bed]      
max_error: 120                
check_gain_time:40           
hysteresis: 5                
heating_gain: 2 

[temperature_fan enclosure] # exhaust fan
sensor_type: temperature_host
pin: PA2
max_temp: 100.0               
target_temp: 60.0             
min_temp: 0
shutdown_speed: 0.0
kick_start_time: 0.5
off_below: 0.19
max_speed: 1.0
min_speed: 0.30
control: pid
pid_Kp: 0.40
pid_Ki: 5.0
pid_Kd: 0.2
pid_deriv_time: 2.0

[gcode_arcs]                       
resolution: 0.01

[led main_led]
white_pin: PA3
hardware_pwm: true
#value:1
cycle_time: 0.010

[idle_timeout]
gcode: _IDLE_TIMEOUT
timeout: 3600

[save_variables]
filename =/home/sovol/printer_data/config/saved_variables.cfg
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

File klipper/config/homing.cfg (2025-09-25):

#####################################################################
#  Homing definition
#####################################################################
[homing_override]
axes: yxz
set_position_z: 0
gcode:
  _INITIALIZE_FROM_DETECTED_TOOL
  {% if printer.probe.last_query  %}
    RESPOND TYPE=echo MSG='Z Probe triggered, cannot home.'
  {% else %}
    #SET_GCODE_OFFSET X=0.0 Y=0.0 Z=0.0
    {% set user = printer['gcode_macro _USER_VARIABLE'] %}
    {% set home_x, home_y, home_z = False, False, False %} ; define what axes need to be homed
    {% if params.X is not defined and params.Y is not defined and params.Z is not defined %} ; G28
      {% set home_x, home_y, home_z = True, True, True %}
    {% else %}
      {% if params.X is defined %}{% set home_x = True %}{% endif %}
      {% if params.Y is defined %}{% set home_y = True %}{% endif %}
      {% if params.Z is defined %}
        {% if 'x' not in printer.toolhead.homed_axes %}{% set home_x = True %}{% endif %} ; check if homed
        {% if 'y' not in printer.toolhead.homed_axes %}{% set home_y = True %}{% endif %} ; check if homed
        {% set home_z = True %}
      {% endif %}
    {% endif %}
    {% if user.hw.mag_probe.ena %} _MAG_PROBE ACTION=GET_STATUS RESPOND=0 {% endif %} ; generate probe state
    _SET_ACC VAL=HOME                                   ; reduce accel and accel_to_decel
    G0 Z{user.homing.z_endstop.hop} F{user.speed.z_hop} ; lift nozzle
    #G0 Z5 F{user.speed.z_hop} ; lift nozzle
    {% if home_y %} _SENSORLESS_HOME_Y {% endif %}                 ; home Y
    {% if home_x %} _SENSORLESS_HOME_X {% endif %}                 ; home X
    {% if home_z %} _HOME_Z            {% endif %}                 ; home Z
    _SET_ACC                                            ; set accel and accel_to_decel back to cfg value
    INITIALIZE_TOOLCHANGER                              ; Initialize tool changer
  {% endif %}

[gcode_macro _SENSORLESS_HOME_X]
gcode:
    {% set HOME_CUR = 0.700 %}
    {% set driver_config = printer.configfile.settings['tmc2209 stepper_x'] %}
    {% set RUN_CUR = driver_config.run_current %}
    #RESPOND TYPE=echo MSG='Sensorless homing X'
    # Set current for sensorless homing
    SET_TMC_CURRENT STEPPER=stepper_x CURRENT={HOME_CUR}
    SET_TMC_CURRENT STEPPER=stepper_y CURRENT={HOME_CUR}
    # Pause to ensure driver stall flag is clear
    G4 P300
    # Home
    G28 X
    # Move away
    G91
    G1 X5 F9600
    G90
    # Set current during print
    SET_TMC_CURRENT STEPPER=stepper_x CURRENT={RUN_CUR}  
    SET_TMC_CURRENT STEPPER=stepper_y CURRENT={RUN_CUR}  

[gcode_macro _SENSORLESS_HOME_Y]
gcode:
    {% set HOME_CUR = 0.700 %}
    {% set driver_config = printer.configfile.settings['tmc2209 stepper_y'] %}
    {% set RUN_CUR = driver_config.run_current %}
    #RESPOND TYPE=echo MSG='Sensorless homing Y'
    # Set current for sensorless homing
    SET_TMC_CURRENT STEPPER=stepper_x CURRENT={HOME_CUR}
    SET_TMC_CURRENT STEPPER=stepper_y CURRENT={HOME_CUR}
    # Pause to ensure driver stall flag is clear
    #G4 P2000
    # Home
    G28 Y
    # Move away
    G91
    G1 Y-5 F9600
    G90
    # Set current during print
    SET_TMC_CURRENT STEPPER=stepper_x CURRENT={RUN_CUR}  
    SET_TMC_CURRENT STEPPER=stepper_y CURRENT={RUN_CUR}  

[gcode_macro _HOME_Z]
description: Helper: z homing
variable_calibrate_z_next: False
gcode:
  {% set user = printer['gcode_macro _USER_VARIABLE'] %}
  ; use -10 as default to insure it error out in case the variable is not existing
  {% set z_endstop = user.homing.z_endstop|default({'x':-10,'y':-10,'z':0, 'hop':0}) %}
  {% if user.hw.mag_probe.ena %}
    {% set probe = printer['gcode_macro _MAG_PROBE'].state|default('unknown')|lower %} ; get probe state
    {% set error = "run \"_MAG_PROBE ACTION=GET_STATUS\"" if probe == 'unknown' 
              else "last dock or undock failed"           if probe == 'error'
              else "not valid"                            if probe is not in ['docked','attached']
              else "" %}
    {% if error|length > 0 %} 
      {action_raise_error("Home&Probe: MagProbe state %s %s" % (error,probe|upper))}
    {% endif %}
  {% endif %}
  {% if user.hw.mag_probe.ena and probe == 'docked' %}
    {action_respond_info("Home&Probe: Probe docked, attach probe first")}
    ATTACH_PROBE                                          ; detach probe
  {% endif %}
  _SET_Z_CURRENT VAL=HOME                                 ; reduce Z current
  G90                                                     ; absolute position
  G0 Y{z_endstop.y} F{user.speed.travel}   ; move to endstop position
  G0 X{z_endstop.x} Y{z_endstop.y} F{user.speed.travel}   ; move to endstop position
  G28 Z                                                   ; home Z
  G0 Z{z_endstop.z} F{user.speed.z_hop/3}                 ; lift toolhead to stop pressing on the pin
  {% if calibrate_z_next %}
    SET_GCODE_VARIABLE MACRO=_HOME_Z VARIABLE=calibrate_z_next VALUE=False
  {% else %}
    _SET_Z_CURRENT                                        ; set Z current back to cfg value
    #G0 Z{user.z_hop} F{user.speed.z_hop}                  ; lift toolhead
    G0 Z5 F{user.speed.z_hop}                  ; lift toolhead
    {% if user.hw.mag_probe.ena and probe == 'docked' %}
      {action_respond_info("Home&Probe: Probe was detached, detach probe last")}
      DETACH_PROBE                                          ; detach probe
    {% endif %}
  {% endif %}
  {% if not printer.gcode_move.absolute_coordinates %} G91 {% endif %} ; set it back to relative

#####################################################################
#  Macros
#####################################################################
## conditional home
[gcode_macro _CG28]
description: Helper: Conditional homing
gcode:
  {% if "xyz" not in printer.toolhead.homed_axes %} G28 {% endif %}

; Depending on the selected tool at the time of homing, the physical Z endstop position is offset.
; This corrects for that using current tool offset.
[gcode_macro _ADJUST_Z_HOME_FOR_TOOL_OFFSET]
gcode:
      G90 ; absolute mode
      G0 Z10 F1000
      {% set tool = printer.toolchanger.tool %}
      {% if tool %}
         {% set tool_z_offset = printer[tool].gcode_z_offset %}
         {% set probe_z_offset = printer.tool_probe_endstop.active_tool_probe_z_offset %}
         SET_KINEMATIC_POSITION Z={10.0+tool_z_offset|float+probe_z_offset|float}
      {% endif %}

[gcode_macro _APPLY_ACTIVE_TOOL_GCODE_OFFSETS]
gcode:
    ; Apply gcode offsets
    {% set tool = printer.toolchanger.tool %}
    {% if tool %}
      SET_GCODE_OFFSET X={printer[tool].gcode_x_offset} Y={printer[tool].gcode_y_offset} Z={printer[tool].gcode_z_offset}
    {% endif %}

[gcode_macro _TAP_PROBE_ACTIVATE]
description: Ensure safe temp for bed probing
gcode:
    {% set max_temp = 150 %}
    {% set actual_temp = printer[params.HEATER].temperature %}
    {% set target_temp = printer[params.HEATER].target %}
    {% if target_temp > max_temp %}
        { action_respond_info('Extruder temperature target of %.1fC is too high, lowering to %.1fC' % (target_temp, max_temp)) }
        SET_HEATER_TEMPERATURE HEATER={params.HEATER} TARGET={ max_temp|int - 5 }
    {% endif %}
    # Temperature target is already low enough, but nozzle may still be too hot.
    {% if actual_temp > max_temp  + 2 %}
        { action_respond_info('Extruder temperature %.1fC is still too high, waiting until below %.1fC' % (actual_temp, max_temp)) }
        TEMPERATURE_WAIT SENSOR={params.HEATER} MAXIMUM={ max_temp }
    {% endif %}
    
[gcode_macro _SET_Z_CURRENT]
description: Helper: Set Z-drive motor current
variable_last_val: 'CONFIG'
gcode:
  {% set val = params.VAL|default('CONFIG') %}
  {% set z_run = printer['gcode_macro _USER_VARIABLE'].homing.z_current       if val == 'HOME'
            else printer.configfile.settings['tmc2209 stepper_z'].run_current if 'tmc2209 stepper_z' in printer.configfile.settings
            else printer.configfile.settings['tmc2660 stepper_z'].run_current if 'tmc2660 stepper_z' in printer.configfile.settings
            else printer.configfile.settings['tmc5160 stepper_z'].run_current if 'tmc5160 stepper_z' in printer.configfile.settings %}
  {% if val != last_val %}
    SET_GCODE_VARIABLE MACRO=_SET_Z_CURRENT VARIABLE=last_val VALUE='"{val}"'
    {% if params.RESPOND|default(printer['gcode_macro _USER_VARIABLE'].respond.z_current)|int == 1 %}
      {action_respond_info("Home&Probe: RunCur %.2fA rms" % z_run|float)}
    {% endif %}
    SET_TMC_CURRENT STEPPER=stepper_z  CURRENT={z_run}
    SET_TMC_CURRENT STEPPER=stepper_z1 CURRENT={z_run}
    SET_TMC_CURRENT STEPPER=stepper_z2 CURRENT={z_run}
    SET_TMC_CURRENT STEPPER=stepper_z3 CURRENT={z_run}
    M400
  {% endif %}
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

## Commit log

2025-09-24 First import
    [DIN Rail holder x2.SLDPRT, DIN Rail holder x2.STL, RSP-500 DIN Bracket low x2.SLDPRT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]
2025-09-24 Added PSU mount photos
2025-09-24 next changes
    [Display stoper.SLDPRT, Display stoper.STL]
2025-09-25 next point
    [cable-organiser_x4.stl]
2025-09-25 next points
    [6x3mm Magnet.SLDPRT, BHCS.SLDASM, Bambulab A1 Wiper.SLDPRT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]
